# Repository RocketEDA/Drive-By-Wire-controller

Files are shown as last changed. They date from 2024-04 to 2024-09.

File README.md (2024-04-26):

# DBW-controller

DISCLAIMER: Please read the LICENSE file. Electronic throttle body control is not for the faint of heart. It can result in injury or death of road users. Test, verify, and test again before using on a road with other people. Understand the software and hardware, how they interact, apply good engineering principles and common sense.
As stated in the LICENSE file, by using this project in any way, you agree to take on full responsibilities to damages caused by this project.

Drive by wire controller, maps throttle to throttle body 1:1 with idle control
PXL_20240426_063848482 MP

For my application I used a Chrysler/mercedes 75mm throttle body with a corvette c6 throttle pedal.
P/N 0280750570
P/N 25835421

SOFTWARE:
Code is fully commented.

Schematic description:
arduino nano handles all the code and control. 
D2 has an input for switch SW2, signaling to enter setup mode
A6 has a potentiometer, handling idle control.
For servo drive a BTS7960 module from amazon is used.

PCA9685 is used for better PWM control. PWM0 and PWM is used for the BTS, the rest are open


Optionally popuplate R11 and R12. The chrylser TB used a HAR3726 magnetic sensor which specifies for a 10k RL


Assembly notes:
The capacitor and terminal blocks will need to moved to the other side on the BTS7960 to clear. I took this opportunity to upsize the capacitor as well, not sure if there's any appreciatable benefit.


J2 and J4 connect to the TB TPS and e-pedal TPS.
Both e-pedal TPS's are positive direction, aka voltage increases as TPS approaches "open"
TB TPS has one signal inverted. To change this the calculation can be modified:


Upon first run, the "setup" switch should be set. Plugin a USB and set baud to 115200 to follow setup instructions. The potentiometer sets idle (minimum) throttle position. The equation is as follows. Insert a DMM probe between GND and IDLE to measure the pot's voltage. The idle % equation is: Idle position % = (IDLE voltage / 5) * (MAX_IDLE_TB_OPEN / 1023) * 100



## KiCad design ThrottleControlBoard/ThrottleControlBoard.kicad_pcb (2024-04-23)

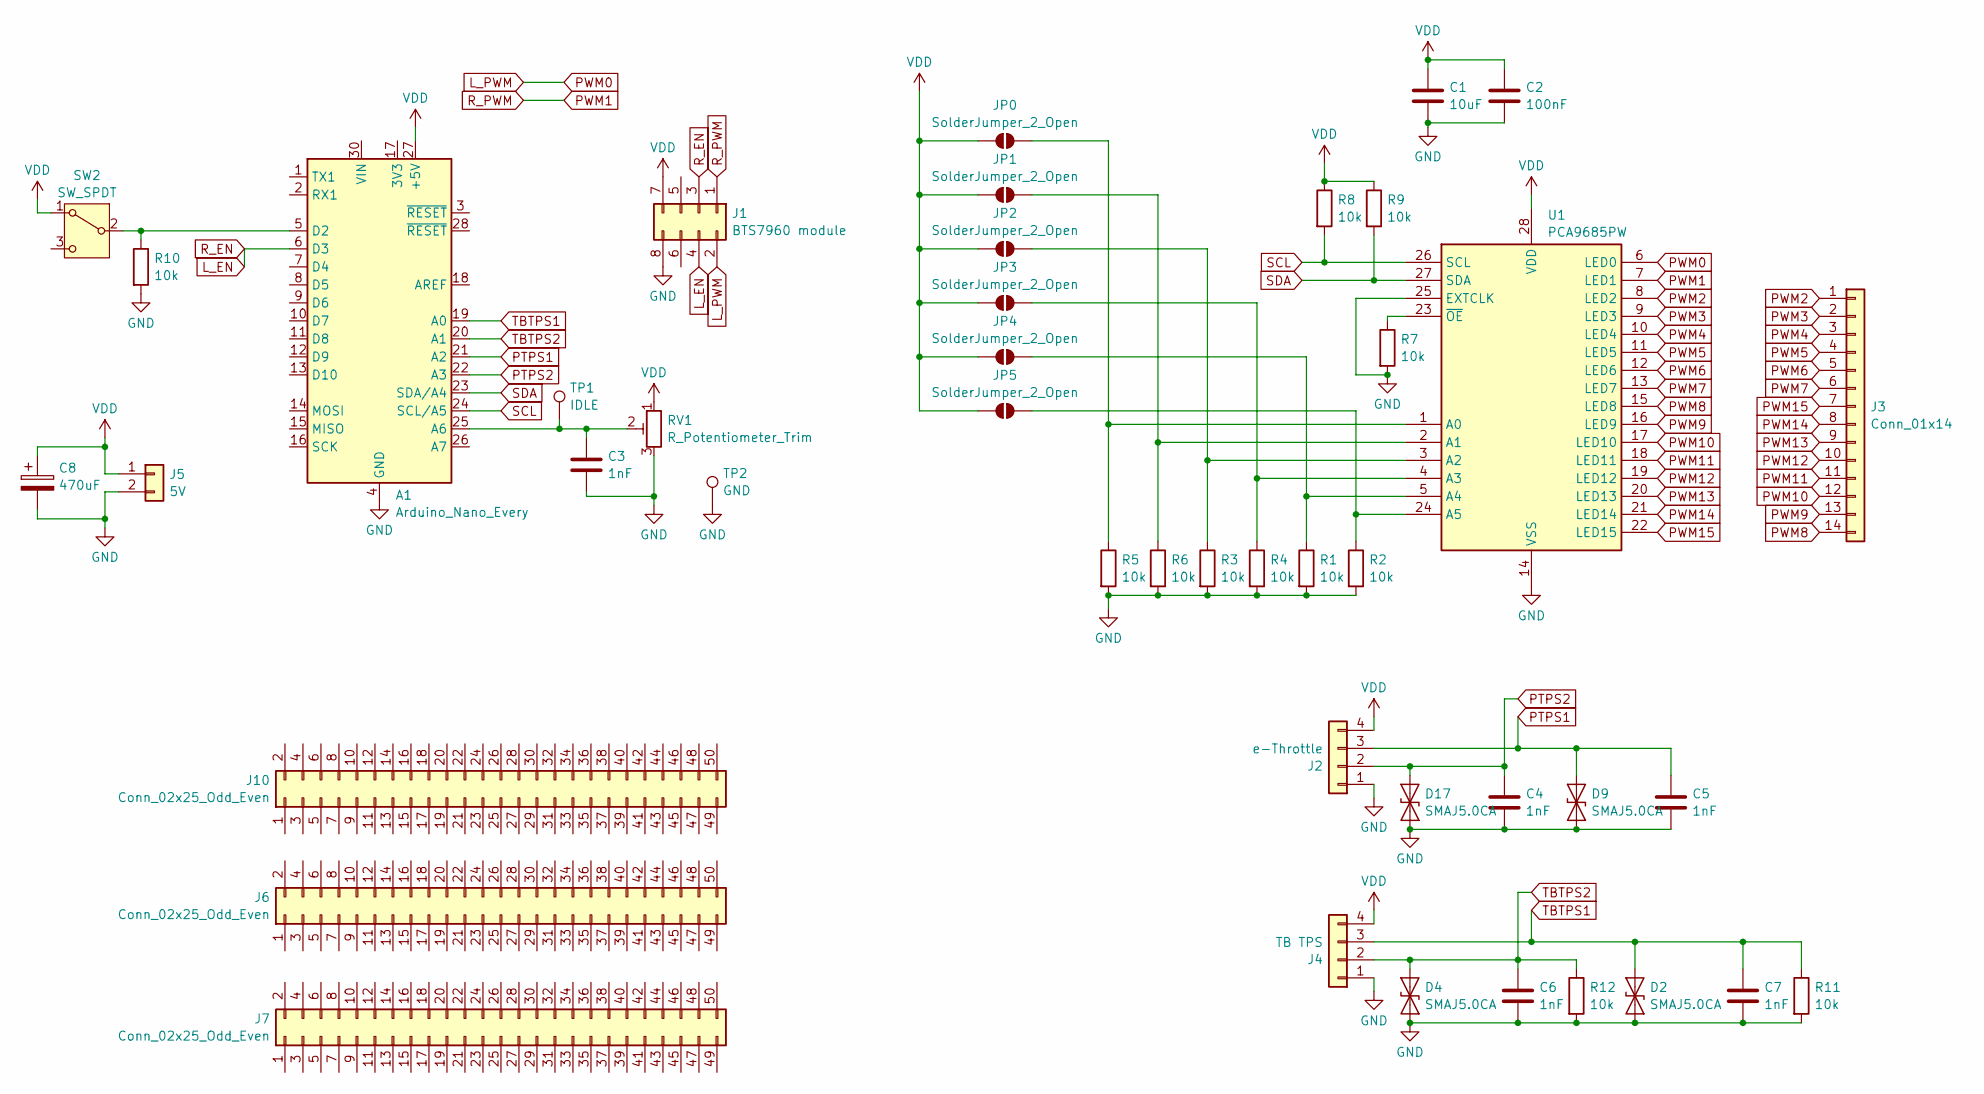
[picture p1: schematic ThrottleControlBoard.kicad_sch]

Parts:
A1: Arduino_Nano_Every; Arduino_Nano
C1: 10uF; C_0805_2012Metric_Pad1.18x1.45mm_HandSolder
C2: 100nF; C_0805_2012Metric_Pad1.18x1.45mm_HandSolder
C3, C4, C5, C6, C7: 1nF; C_0805_2012Metric_Pad1.18x1.45mm_HandSolder
C8: 470uF; CP_Radial_D8.0mm_P3.50mm
D2, D4, D9, D17: SMAJ5.0CA; D_SMA
J1: BTS7960 module; PinHeader_2x04_P2.54mm_Vertical
J2: e-Throttle; TerminalBlock_Altech_AK300-4_P5.00mm
J3: Conn_01x14; PinHeader_1x14_P2.54mm_Vertical
J4: TB TPS; TerminalBlock_Altech_AK300-4_P5.00mm
J5: 5V; TerminalBlock_Altech_AK300-2_P5.00mm
J6, J7, J10: Conn_02x25_Odd_Even; PinHeader_2x25_P2.54mm_Vertical
JP0, JP1, JP2, JP3, JP4, JP5: SolderJumper_2_Open; SolderJumper-2_P1.3mm_Open_TrianglePad1.0x1.5mm
R1, R2, R3, R4, R5, R6, R7, R8, R9, R10, R11, R12: 10k; R_0603_1608Metric_Pad0.98x0.95mm_HandSolder
RV1: R_Potentiometer_Trim; PinHeader_1x03_P2.54mm_Vertical
SW2: SW_SPDT; PinHeader_1x03_P2.54mm_Vertical
TP1: IDLE; TestPoint_Loop_D3.80mm_Drill2.5mm
TP2: GND; TestPoint_Loop_D3.80mm_Drill2.5mm
U1: PCA9685PW; TSSOP-28_4.4x9.7mm_P0.65mm

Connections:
GND: A1.4 (GND), A1.29 (GND), C1.2, C2.2, C3.2, C4.2, C5.2, C6.2, C7.2, C8.2, D2.1 (A1), D4.1 (A1), D9.1 (A1), D17.1 (A1), J1.8, J2.1, J4.1, J5.2, R1.2, R2.2, R3.2, R4.2, R5.2, R6.2, R7.2, R10.2, R11.2, R12.2, RV1.3, TP2.1, U1.14 (VSS), U1.25 (EXTCLK)
L_EN: A1.6 (D3), J1.3, J1.4
L_PWM: J1.2, U1.6 (LED0)
unnamed: A1.25 (A6), C3.1, RV1.2, TP1.1
unnamed: A1.5 (D2), R10.1, SW2.2 (B)
unnamed: JP0.2 (B), R5.1, U1.1 (A0)
unnamed: JP1.2 (B), R6.1, U1.2 (A1)
unnamed: JP2.2 (B), R3.1, U1.3 (A2)
unnamed: JP3.2 (B), R4.1, U1.4 (A3)
unnamed: JP4.2 (B), R1.1, U1.5 (A4)
unnamed: JP5.2 (B), R2.1, U1.24 (A5)
unnamed: R7.1, U1.23 (~OE)
PTPS1: A1.21 (A2), C5.1, D9.2 (A2), J2.3
PTPS2: A1.22 (A3), C4.1, D17.2 (A2), J2.2
PWM1: J1.1, U1.7 (LED1)
PWM2: J3.1, U1.8 (LED2)
PWM3: J3.2, U1.9 (LED3)
PWM4: J3.3, U1.10 (LED4)
PWM5: J3.4, U1.11 (LED5)
PWM6: J3.5, U1.12 (LED6)
PWM7: J3.6, U1.13 (LED7)
PWM8: J3.14, U1.15 (LED8)
PWM9: J3.13, U1.16 (LED9)
PWM10: J3.12, U1.17 (LED10)
PWM11: J3.11, U1.18 (LED11)
PWM12: J3.10, U1.19 (LED12)
PWM13: J3.9, U1.20 (LED13)
PWM14: J3.8, U1.21 (LED14)
PWM15: J3.7, U1.22 (LED15)
SCL: A1.24 (SCL/A5), R8.2, U1.26 (SCL)
SDA: A1.23 (SDA/A4), R9.2, U1.27 (SDA)
TBTPS1: A1.19 (A0), C7.1, D2.2 (A2), J4.3, R11.1
TBTPS2: A1.20 (A1), C6.1, D4.2 (A2), J4.2, R12.1
VDD: A1.27 (+5V), C1.1, C2.1, C8.1, J1.7, J2.4, J4.4, J5.1, JP0.1 (A), JP1.1 (A), JP2.1 (A), JP3.1 (A), JP4.1 (A), JP5.1 (A), R8.1, R9.1, RV1.1, SW2.1 (A), U1.28 (VDD)

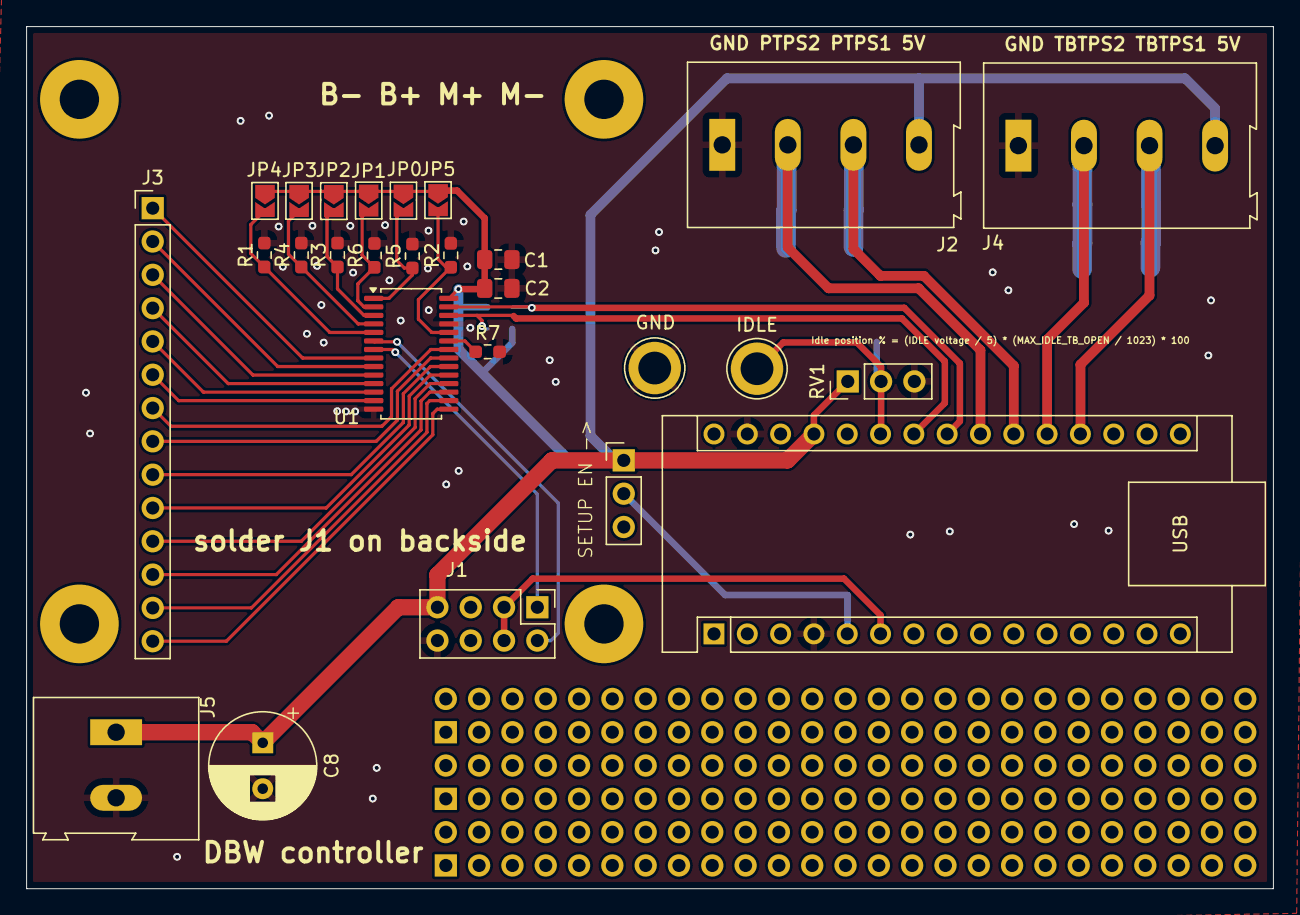
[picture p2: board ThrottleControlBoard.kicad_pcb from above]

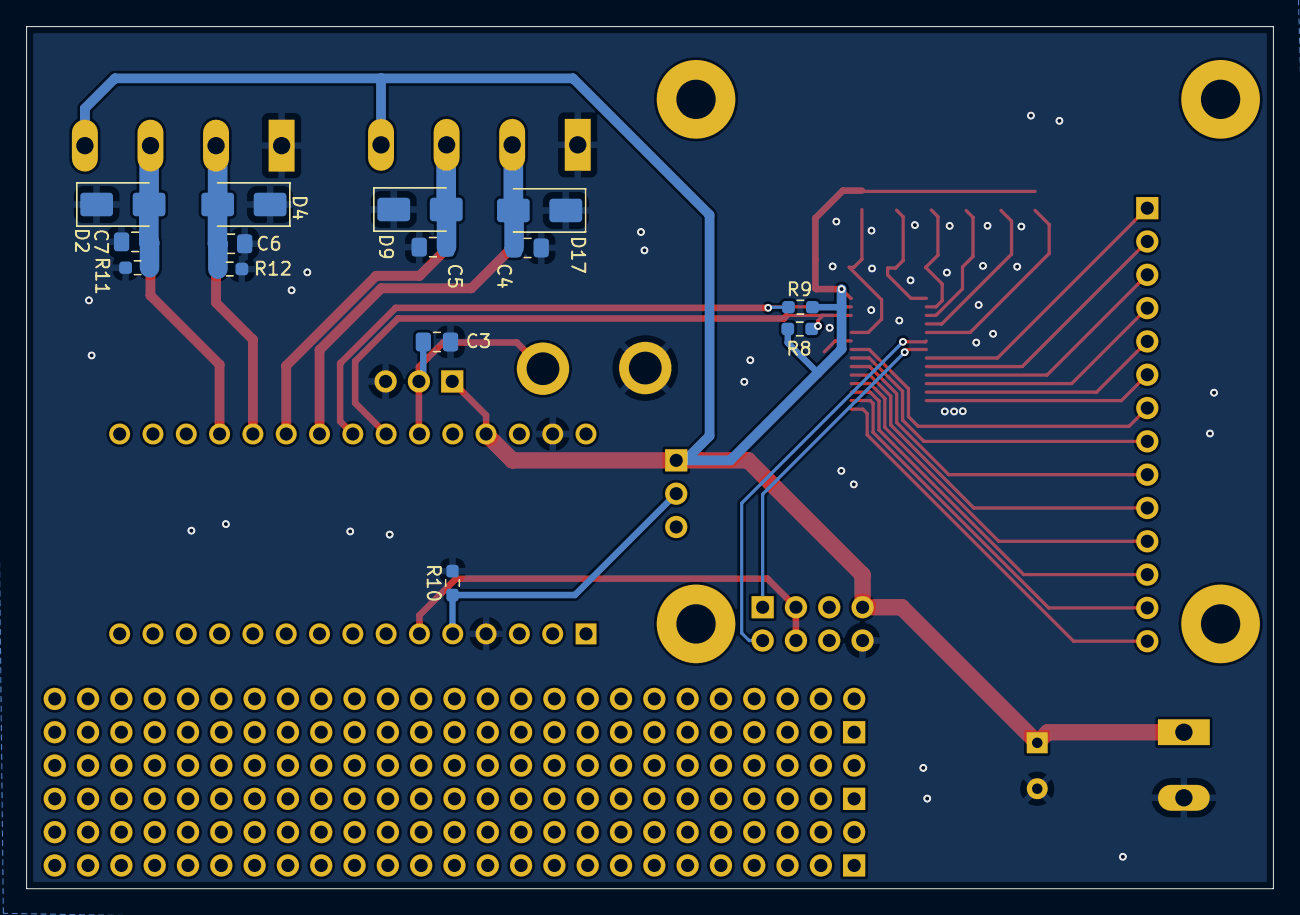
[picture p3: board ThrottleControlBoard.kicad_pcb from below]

Board: 2 copper layers, 95.1 x 65.7 mm, 44 parts (14 on the bottom side), 34 nets.

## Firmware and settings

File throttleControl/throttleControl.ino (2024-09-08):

#include <arduino-timer.h>
//#include <Adafruit_ADS1X15.h>
#include <Wire.h>
#include <Adafruit_PWMServoDriver.h>

#include <EEPROM.h>


////////////////////////////////////Throttle Body//////////////////////////////////////
#define PWM_FREQ 500    //tb pwm frequency

//PCA9685 pins
#define LPWM_pin 0      //PWM pin on PCA9685
#define RPWM_pin 1      //PWM pin on PCA9685
#define EN_pin 3        //R_EN/L_EN tied together
//#define RIS_pin         //overcurrent alarm right
//#define LIS_pin         //overcurrent alarm right

#define PROPGAIN 20 //proportional gain, motor force (12b) = (TB TPS(10b) - pedal pos (10b)) * PROPGAIN
                    //decrease if oscillating, increase for better throttle response and precision

#define MINPWM 1600     //minimum PWM for the motor to having action
#define PWMFREQ 500     //servo pwm frequency

//////////////////////////////////////TPS///////////////////

//TPS 1/2 maximum variation -- used for error checking if one redundant sensor has failed
#define TBTPS_var 200
#define PTPS_var 300

//throttle body pot pins
#define TBTPS1_pin A0
#define TBTPS2_pin A1

//e-pedal pot pins
#define PTPS1_pin A2
#define PTPS2_pin A3

//min throttle idle pot pin
#define IDLE_POT_pin A6

//maximum possible throttle plate open at idle (0-1023)
#define MAX_IDLE_TB_OPEN 200

//////////////////////////////////////Other
//programming macros
#define OPEN 1
#define CLOSE 0

#define INUM 100  //control loop interval in uS

#define EEPROM_ADDR 100   //address to store pedal TPS values
#define SETUP_pin 2       //setup switch, apply 5V to activate

//throttle body tps sensor
float tbtps1_val = 0;
float tbtps2_val = 0;

//pedal tps sensor
float ptps1_val = 0;
float ptps2_val = 0;

//throttle body TPS max/min values
float tbtps1_OPEN = 0;
float tbtps1_CLOSE = 0;
float tbtps1_range = 0;   //range = open-close. precalculate for faster runtime

float tbtps2_OPEN = 0;
float tbtps2_CLOSE = 0;
float tbtps2_range = 0;   //range = open-close. precalculate for faster runtime

//pedal TPS max/min values
float ptps1_OPEN = 0;
float ptps1_CLOSE = 0;
float ptps1_range = 0;   //range = open-close. precalculate for faster runtime

float ptps2_OPEN = 0;
float ptps2_CLOSE = 0;
float ptps2_range = 0;   //range = open-close. precalculate for faster runtime

float idle_pos = 0;   //minimum throttle position

float throttlePos = 0;   //throttle pedal position average reading

float mot_pwm = 0;  //motor force control follows writeMot convention

float tbAvg = 0; //throttle body position average reading


Adafruit_PWMServoDriver pwm = Adafruit_PWMServoDriver();

Timer<3, micros> u_timer;

/*
   readTBTPS
   directly reads throttle body TPS
   raw value
*/
void readTBTPS()
{
  tbtps1_val = analogRead(TBTPS1_pin);
  tbtps2_val = analogRead(TBTPS2_pin);
}

/*
   readPTPS
   directly reads pedal TPS
   raw value
*/
void readPTPS()
{
  //invert if pins are inversed
  ptps1_val = analogRead(PTPS2_pin);
  ptps2_val = analogRead(PTPS1_pin);
}
/*
   calculateTBTPS
   abstracts readTBTPS
   calculates tbAvg
*/
bool calculateTBTPS()
{
  readTBTPS();
  //read and calculate current motor position
  float tbTemp1 = abs(((tbtps1_val - tbtps1_CLOSE) * 1024) / tbtps1_range);
  float tbTemp2 = abs(((tbtps2_CLOSE - tbtps2_val) * 1024) / tbtps2_range);
  //average between the two, use
  tbAvg = abs((tbTemp1 + tbTemp2) / 2);
  //Serial.println("tbtemp1: " + String(tbTemp1) + "\ttbtemp2: " +  String(tbTemp2));
  if (abs(tbTemp1 - tbTemp2) > TBTPS_var)
  {
    //error
    Serial.println("readTPS: ERROR INVALID TBTPS " + String(tbTemp1) + "\t" +  String(tbTemp2));
    //read and calculate current motor position
    
    while (1)
    {
      emergencyStop();
    }
    
  }
  return true;
}

/*
   calculateTPTPS
   abstracts readPTPS
   calculates throttlePos
*/
bool calculatePTPS()
{
  readPTPS();
  //pedal tps sensor
  //read and calculate current pedal position, based on range, pos close and pos open
  float pTemp1 = abs(((ptps1_val - ptps1_CLOSE) * 1023) / ptps1_range);
  float pTemp2 = abs(((ptps2_val - ptps2_CLOSE) * 1023) / ptps2_range);
  throttlePos = idle_pos + ((abs((pTemp1 + pTemp2) / 2.0) / 1023.0) * (1023 - idle_pos));    //average and scale with idle position
  throttlePos = constrain(throttlePos, 0, 1023);
  if (abs(pTemp1 - pTemp2) > PTPS_var)
  {
    //error
    Serial.println("readTPS: ERROR INVALID PTPS " + String(pTemp1) + "\t" +  String(pTemp2));
    //read and calculate current motor position
    
    while (1)
    {
      emergencyStop();
    }
    
  }
  //Serial.println(String(pTemp1) + "\t" + String(pTemp2) + "\t" + String(throttlePos));
  return true;
}

/*
   emergencyStop
   call this when in error state
   concentrates the numbers in one area, decreases chance for error
*/
void emergencyStop()
{
  digitalWrite(EN_pin, LOW);
}
/*
   writeMot
   writes to motor
   val: 13 bit, 0-4095 is close, 4096 is relax, 4097-8192 is open
*/
void writeMot(float val)
{
  /*
     RPWM+ LPWM- to open
  */
  if (val > 8192 || val < 0)
  {
    Serial.println("writeMot: ERROR VAL EXCEEDED " + String(val));
    emergencyStop();
    while (1);
  }
  else if (val < 4096)
  {
    //close
    digitalWrite(EN_pin, HIGH);
    pwm.setPWM(RPWM_pin, 0, 0);
    pwm.setPWM(LPWM_pin, 0, 4095 - val);
    //Serial.println("CLOSE: " + String(val));
  }
  else if (val > 4096)
  {
    //open
    digitalWrite(EN_pin, HIGH);
    pwm.setPWM(RPWM_pin, 0, val - 4097);
    pwm.setPWM(LPWM_pin, 0, 0);
    //Serial.println("OPEN: " + String(val));
  }
  else if (val == 4096)
  {
    //relax
    digitalWrite(EN_pin, LOW);
    pwm.setPWM(RPWM_pin, 0, 0);
    pwm.setPWM(LPWM_pin, 0, 0);
    //Serial.println("HOLD: " + String(val));
  }

}

/*
   abstracts writeMot
   sets position of throttle body based on global throttlePos
   interval controller so call on interval
*/
bool setPos()
{
  if (tbAvg < throttlePos)
  {
    mot_pwm = 4096 + (PROPGAIN * (throttlePos - tbAvg));
  }
  else if (tbAvg > throttlePos)
  {
    mot_pwm = 4096 + (PROPGAIN * (throttlePos - tbAvg));
  }
  mot_pwm = constrain(mot_pwm, 0, 8192);
  //Serial.println(String(mot_pwm) + "\t" + String(tbAvg) + "\t" + String(throttlePos));
  //Serial.println(String(throttlePos - tbAvg));
  writeMot(mot_pwm);
  return true;
}
/*
   read max/min TB values
*/
void initSequence()
{
  Serial.println("initialization sequence");
  //////////////////////////////TB setup
  //open motor
  writeMot(8191);
  delay(500);
  //while(1);
  //read TB TPS values
  readTBTPS();
  tbtps1_OPEN = tbtps1_val;
  tbtps2_OPEN = tbtps2_val;

  //close motor
  writeMot(0);
  delay(500);

  //read TB TPS values
  readTBTPS();
  tbtps1_CLOSE = tbtps1_val;
  tbtps2_CLOSE = tbtps2_val;

  //calculate ranges
  tbtps1_range = abs(tbtps1_OPEN - tbtps1_CLOSE);
  tbtps2_range = abs(tbtps2_OPEN - tbtps2_CLOSE);

  Serial.println("TPS1OPEN: " + String(tbtps1_OPEN) + " TPS1CLOSE: " + String(tbtps1_CLOSE) + " TPS2OPEN: " + String(tbtps2_OPEN) + " TPS2CLOSE: " + String(tbtps2_CLOSE));
  //Serial.println("tbtps1_range: " + String(tbtps1_range) + " tbtps2_range: " + String(tbtps2_range));
  writeMot(4096); //relax motor


  /*
     checks if setup switch (pin) is pulled HIGH
     allows setting calibration values if it is
     else reads values from eeprom
  */
  bool setup_en = digitalRead(SETUP_pin);
  Serial.println("Setup mode: " + String(setup_en));
  if (setup_en)
  {
    //enter setup
    Serial.println("Push throttle all the way then release. Do this a few times to capture the range");
    readPTPS();
    idle_pos = analogRead(IDLE_POT_pin);
    ptps1_OPEN = ptps1_val;
    ptps1_CLOSE = ptps1_val;
    ptps2_OPEN = ptps2_val;
    ptps2_CLOSE = ptps2_val;
    while (setup_en)
    {
      readPTPS();
      //find max/mins
      if (ptps1_val > ptps1_OPEN)
      {
        ptps1_OPEN = ptps1_val;
      }
      if (ptps1_val < ptps1_CLOSE)
      {
        ptps1_CLOSE = ptps1_val;
      }
      if (ptps2_val > ptps2_OPEN)
      {
        ptps2_OPEN = ptps2_val;
      }
      if (ptps2_val < ptps2_CLOSE)
      {
        ptps2_CLOSE = ptps2_val;
      }
      //set test idle position to throttlePos, write to motor
      throttlePos = (float(analogRead(IDLE_POT_pin)) * MAX_IDLE_TB_OPEN) / 1023;
      calculateTBTPS();
      setPos();
      setup_en = digitalRead(SETUP_pin);
    }
    writeMot(4096);  //relax motor
    //save to eeprom   EEPROM_ADDR
    Serial.println("Writing EEPROM...");
    EEPROM.put(EEPROM_ADDR, ptps1_OPEN);                            //pedal1 open
    EEPROM.put(EEPROM_ADDR + sizeof(float), ptps1_CLOSE);           //pedal1 close
    EEPROM.put(EEPROM_ADDR + (2 * sizeof(float)), ptps2_OPEN);      //pedal2 open
    EEPROM.put(EEPROM_ADDR + (3 * sizeof(float)), ptps2_CLOSE);     //pedal2 close
    EEPROM.put(EEPROM_ADDR + (4 * sizeof(float)), throttlePos);     //idle throttle position

    Serial.println("ptps1_OPEN: " + String(ptps1_OPEN));
    Serial.println("ptps1_CLOSE: " + String(ptps1_CLOSE));
    Serial.println("ptps2_OPEN: " + String(ptps2_OPEN));
    Serial.println("ptps2_CLOSE: " + String(ptps2_CLOSE));
    Serial.println("IDLE: " + String(throttlePos));
  }
  Serial.println("Reading EEPROM...");
  //not setup mode, read from eeprom
  EEPROM.get(EEPROM_ADDR, ptps1_OPEN);                            //pedal1 open
  EEPROM.get(EEPROM_ADDR + sizeof(float), ptps1_CLOSE);           //pedal1 close
  EEPROM.get(EEPROM_ADDR + (2 * sizeof(float)), ptps2_OPEN);      //pedal2 open
  EEPROM.get(EEPROM_ADDR + (3 * sizeof(float)), ptps2_CLOSE);     //pedal2 close
  EEPROM.get(EEPROM_ADDR + (4 * sizeof(float)), idle_pos);     //idle throttle position
  //calculate ranges
  ptps1_range = abs(ptps1_OPEN - ptps1_CLOSE);
  ptps2_range = abs(ptps2_OPEN - ptps2_CLOSE);

  Serial.println("ptps1_OPEN: " + String(ptps1_OPEN));
  Serial.println("ptps1_CLOSE: " + String(ptps1_CLOSE));
  Serial.println("ptps2_OPEN: " + String(ptps2_OPEN));
  Serial.println("ptps2_CLOSE: " + String(ptps2_CLOSE));
  Serial.println("ptps1_range: " + String(ptps1_range));
  Serial.println("ptps2_range: " + String(ptps2_range));
  Serial.println("IDLE: " + String(idle_pos));
}


void setup() {
  Serial.begin(115200);
  pwm.begin();
  pwm.setOscillatorFrequency(25000000);
  pwm.setPWMFreq(PWMFREQ);
  Wire.setClock(400000);

  pinMode(EN_pin, OUTPUT);
  pinMode(SETUP_pin, INPUT);
  initSequence();
  //u_timer.every(INUM, calculateTBTPS);
  //u_timer.every(INUM, calculatePTPS);
  //u_timer.every(INUM, setPos);
}
void loop() {
  delayMicroseconds(INUM);
  calculateTBTPS();
  calculatePTPS();
  setPos();
}

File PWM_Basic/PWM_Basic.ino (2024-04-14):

/****************************************************************************************************************************
  PWM_Basic.ino

  For AVR-based boards  (UNO, Nano, Mega, 32U4, 16U4, etc. )
  Written by Khoi Hoang

  Built by Khoi Hoang https://github.com/khoih-prog/AVR_PWM
  Licensed under MIT license

  This is pure hardware-based PWM
*****************************************************************************************************************************/
/******************************************************************************************************************************
  // For UNO / Nano
  Timer0 ( 8-bit) used by delay(), millis() and micros(), and PWM generation on pins 5 (6 not usable)
  Timer1 (16-bit) used by the Servo.h library and PWM generation on pins 9 and 10
  Timer2 ( 8-bit) used by Tone() and PWM generation on pins 3 and 11
  // For Mega
  Timer0 ( 8-bit) used by delay(), millis() and micros(), and PWM generation on pins 4 (13 not usable)
  Timer1 (16-bit) used by the Servo.h library and PWM generation on pins 11, 12
  Timer2 ( 8-bit) used by Tone() and PWM generation on pins 9 and 10
  Timer3 (16-bit) used by PWM generation on pins  2,  3 and  5
  Timer4 (16-bit) used by PWM generation on pins  6,  7 and  8
  Timer5 (16-bit) used by PWM generation on pins 44, 45 and 46

  ////////////////////////////////////////////
  // For Mega (2, 3, 4, 5, 6, 7, 8, 9, 10, 11, 12, 13, 44, 45, 46)
  Pin  2 => TIMER3B   // PE 4 ** 2  ** PWM2
  Pin  3 => TIMER3C   // PE 5 ** 3  ** PWM3
  Pin  4 => TIMER0B   // PG 5 ** 4  ** PWM4
  Pin  5 => TIMER3A   // PE 3 ** 5  ** PWM5
  Pin  6 => TIMER4A   // PH 3 ** 6  ** PWM6
  Pin  7 => TIMER4B   // PH 4 ** 7  ** PWM7
  Pin  8 => TIMER4C   // PH 5 ** 8  ** PWM8
  Pin  9 => TIMER2B   // PH 6 ** 9  ** PWM9
  Pin 10 => TIMER2A   // PB 4 ** 10 ** PWM10
  Pin 11 => TIMER1A   // PB 5 ** 11 ** PWM11
  Pin 12 => TIMER1B   // PB 6 ** 12 ** PWM12
  Pin 13 => TIMER0A   // PB 7 ** 13 ** PWM13
  Pin 44 => TIMER5C   // PL 5 ** 44 ** D44
  Pin 45 => TIMER5B   // PL 4 ** 45 ** D45
  Pin 46 => TIMER5A   // PL 3 ** 46 ** D46
  ////////////////////////////////////////////
  // For 32u4 (3, 5, 6, 9, 10, 11, 13)
  Pin  3 => TIMER0B
  Pin  5 => TIMER3A
  Pin  6 => TIMER4D
  Pin  9 => TIMER1A
  Pin 10 => TIMER1B
  Pin 11 => TIMER0A
  Pin 13 => TIMER4A
  ////////////////////////////////////////////
  // For UNO, Nano (3, 5, 6, 9, 10, 11)
  Pin  3 => TIMER2B,
  Pin  5 => TIMER0B
  Pin  6 => TIMER0A
  Pin  9 => TIMER1A
  Pin 10 => TIMER1B
  Pin 11 => TIMER2(A)
******************************************************************************************************************************/

#define _PWM_LOGLEVEL_       4

#include "AVR_PWM.h"

  // Pins tested OK on Nano / UNO
  //#define pinToUse      9            // Timer1A on UNO, Nano, etc
  //#define pinToUse     10            // Timer1B on UNO, Nano, etc
  //#define pinToUse      5               // Timer0B on UNO, Nano, e
#define pinToUse       3            // Timer2B on UNO, Nano, etc

//creates pwm instance
AVR_PWM* PWM_Instance;

float frequency;
float dutyCycle;

void setup()
{
  Serial.print(F("\nStarting PWM_Basic on "));
  Serial.println(BOARD_NAME);
  Serial.println(AVR_PWM_VERSION);

  //assigns PWM frequency of 20 KHz and a duty cycle of 0%
  PWM_Instance = new AVR_PWM(pinToUse, 20000, 0);
}

void loop()
{
  //delay(10000);
  frequency = 500;    //20000;
  dutyCycle = 20;     //90;

  PWM_Instance->setPWM(pinToUse, frequency, dutyCycle);

  delay(10000);
  dutyCycle = 300;

  PWM_Instance->setPWM(pinToUse, frequency, dutyCycle);

  delay(10000);
}

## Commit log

2024-04-14 initial commit
    8 bit servo control working with l298
    [Book1.xlsx]
2024-04-18 working code with BTS
    test showed very good results
    [Book1.xlsx]
2024-04-22 code implementations completed
    EEPROM save throttle position state, save idle based on pot
    enter setup option upon startup
2024-04-23 PCB done
    [ThrottleControlBoard.kicad_pcb, ThrottleControlBoard.kicad_sch]
2024-04-23 DRC and vias fixed
    [ThrottleControlBoard.kicad_pcb]
2024-04-23 gerbers exported
    [ThrottleControlBoard-B_Cu.gbr, ThrottleControlBoard-B_Mask.gbr, ThrottleControlBoard-B_Paste.gbr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]
2024-04-26 idle position not setting issue fixed
    [throttleControl.ino]
